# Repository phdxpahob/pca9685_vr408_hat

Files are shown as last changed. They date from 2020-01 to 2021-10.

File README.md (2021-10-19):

# pca9685_vr408

This is a Raspberry Pi Hat with PCA9685PW. Design is based on the original Adafruit 16-Channel 12-bit PWM/Servo Driver with I2C interface, adapted for velleman spider robots. 

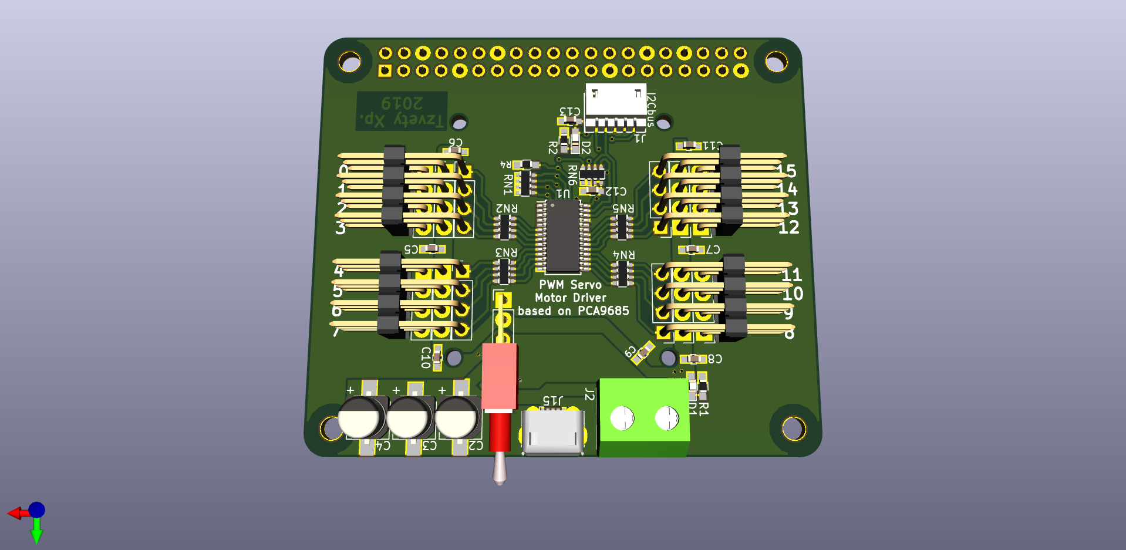
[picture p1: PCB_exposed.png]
PCB without camera stand
 

# WARNING

In revision A, there is an error in the design, VDD of the IC is not connected to the 3.3V rail of the Raspberry PI. This could be done using a wire bridge between the I2C Bus connector and the Via near C12. This is fixed in the current revision.

# Features and benefits:

- Both USB micro-B or terminal block power; 
- Can be powered directly from powerbank or another Pi HAT. 
- Split motor supply, extra capacitors to improve EMC. Tested with servos on all channels and the hat does not reset the Pi.
- Solder jumpers to change I2C address.
- Compatible with Adafruit libraries
- Header connects directly to the I2C pins & GPIO04 for O̅E̅ (Output enable). Even if GPIO is not configured the board is in output enable mode.
- Room for camera stand. (3D model is cam_stand.wrl)

# Limitations:

- No Reverse polarity protection! Keep in mind how you wire the terminal block!

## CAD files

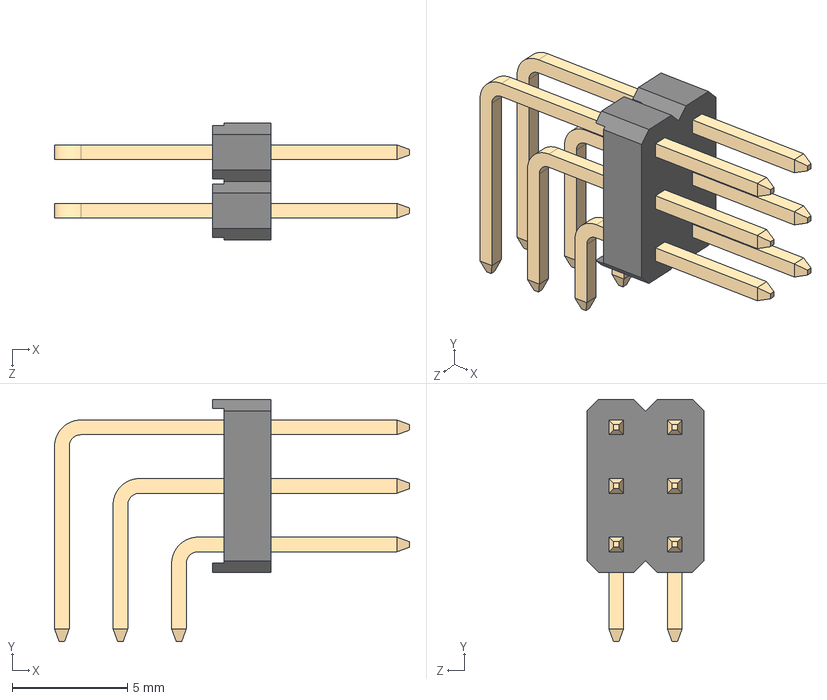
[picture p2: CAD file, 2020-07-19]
BB02-HL061-XB1-6030R0-6T_rev1.6.STEP
15.4 x 10.5 x 5.08 mm
BB02-HL - housing-6p
BB02-HL- Short RA type pin-A=6.0mm,B=3.0mm x 2
BB02-HL- Mid RA type pin-A=6.0mm,B=3.0mm x 2
BB02-HL-Long RA type pin-A=6.0mm,B=3.0mm x 2

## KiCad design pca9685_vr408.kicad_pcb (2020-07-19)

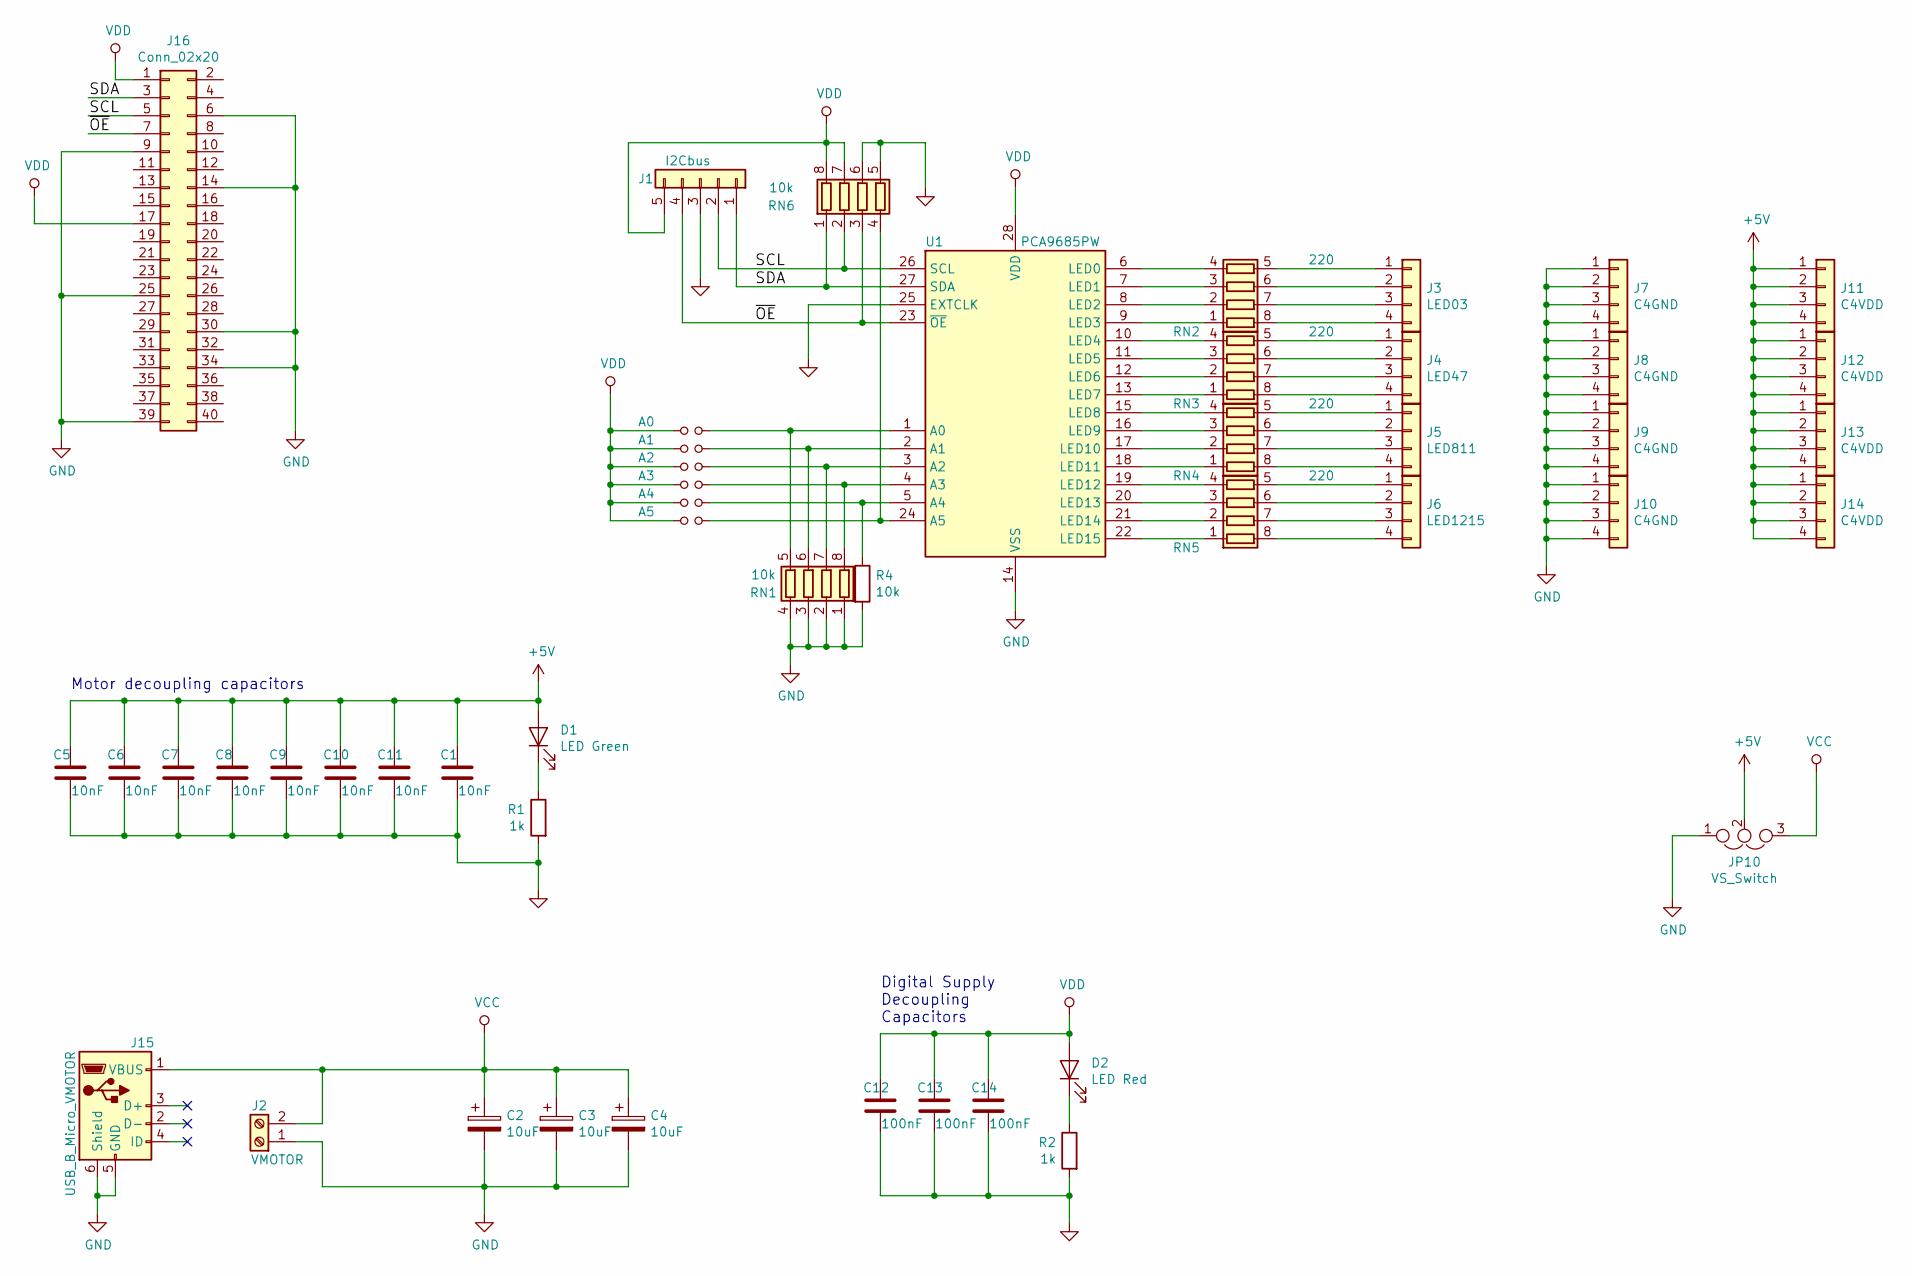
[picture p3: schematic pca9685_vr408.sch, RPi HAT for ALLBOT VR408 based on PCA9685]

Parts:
A0: A0; SolderJumper_Triangular_0603
A1: A1; SolderJumper_Triangular_0603
A2: A2; SolderJumper_Triangular_0603
A3: A3; SolderJumper_Triangular_0603
A4: A4; SolderJumper_Triangular_0603
A5: A5; SolderJumper_Triangular_0603
C1, C5, C6, C7, C8, C9, C10, C11: 10nF; C_0603_HandSoldering
C2, C3, C4: 10uF; CP_Elec_5x5.3
C12, C13, C14: 100nF; C_0603_HandSoldering
D1: LED Green; LED_0603_HandSoldering
D2: LED Red; LED_0603_HandSoldering
J1: I2Cbus; df13-5p-125ds
J2: VMOTOR; TerminalBlock_bornier-2_P5.08mm
J3: LED03; Pin_Header_Straight_1x04_Pitch2.54mm
J4: LED47; Pin_Header_Straight_1x04_Pitch2.54mm
J5: LED811; Pin_Header_Straight_1x04_Pitch2.54mm
J6: LED1215; Pin_Header_Straight_1x04_Pitch2.54mm
J7, J8, J9, J10: C4GND; Pin_Header_Straight_1x04_Pitch2.54mm
J11, J12, J13, J14: C4VDD; Pin_Header_Straight_1x04_Pitch2.54mm
J15: USB_B_Micro_VMOTOR; USB_Micro-B_Molex-105017-0001
J16: Conn_02x20; PinSocket_2x20_P2.54mm_Vertical
JP10: VS_Switch; Pin_Header_Straight_1x03_Pitch2.54mm
R1, R2: 1k; R_0603_HandSoldering
R4: 10k; R_0603_HandSoldering
RN1, RN6: 10k; R_Array_Convex_4x0603
RN2, RN3, RN4, RN5: 220; R_Array_Convex_4x0603
U1: PCA9685PW; TSSOP-28_4.4x9.7mm_Pitch0.65mm

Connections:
+5V: C1.1, C5.1, C6.1, C7.1, C8.1, C9.1, C10.1, C11.1, D1.2 (A), J11.1, J11.2, J11.3, J11.4, J12.1, J12.2, J12.3, J12.4, J13.1, J13.2, J13.3, J13.4, J14.1, J14.2, J14.3, J14.4, JP10.2
/SCL: J1.2, J16.5, RN6.2 (R2.1), U1.26 (SCL)
/SDA: J1.1, J16.3, RN6.1 (R1.1), U1.27 (SDA)
/~OE~: J1.4, J16.7, RN6.3 (R3.1), U1.23 (~OE)
GND: C1.2, C2.2, C3.2, C4.2, C5.2, C6.2, C7.2, C8.2, C9.2, C10.2, C11.2, C12.2, C13.2, C14.2, J1.3, J2.1, J7.1, J7.2, J7.3, J7.4, J8.1, J8.2, J8.3, J8.4, J9.1, J9.2, J9.3, J9.4, J10.1, J10.2, J10.3, J10.4, J15.5 (GND), J15.6 (Shield), J16.6, J16.9, J16.14, J16.25, J16.30, J16.34, J16.39, JP10.1, R1.2, R2.2, R4.2, RN1.1 (R1.1), RN1.2 (R2.1), RN1.3 (R3.1), RN1.4 (R4.1), RN6.5 (R4.2), RN6.6 (R3.2), U1.14 (VSS), U1.25 (EXTCLK)
unnamed: A0.2, RN1.5 (R4.2), U1.1 (A0)
unnamed: A1.2, RN1.6 (R3.2), U1.2 (A1)
unnamed: A2.2, RN1.7 (R2.2), U1.3 (A2)
unnamed: A3.2, RN1.8 (R1.2), U1.4 (A3)
unnamed: A4.2, R4.1, U1.5 (A4)
unnamed: A5.2, RN6.4 (R4.1), U1.24 (A5)
unnamed: D1.1 (K), R1.1
unnamed: D2.1 (K), R2.1
unnamed: J3.1, RN2.5 (R4.2)
unnamed: J3.2, RN2.6 (R3.2)
unnamed: J3.3, RN2.7 (R2.2)
unnamed: J3.4, RN2.8 (R1.2)
unnamed: J4.1, RN3.5 (R4.2)
unnamed: J4.2, RN3.6 (R3.2)
unnamed: J4.3, RN3.7 (R2.2)
unnamed: J4.4, RN3.8 (R1.2)
unnamed: J5.1, RN4.5 (R4.2)
unnamed: J5.2, RN4.6 (R3.2)
unnamed: J5.3, RN4.7 (R2.2)
unnamed: J5.4, RN4.8 (R1.2)
unnamed: J6.1, RN5.5 (R4.2)
unnamed: J6.2, RN5.6 (R3.2)
unnamed: J6.3, RN5.7 (R2.2)
unnamed: J6.4, RN5.8 (R1.2)
unnamed: RN2.1 (R1.1), U1.9 (LED3)
unnamed: RN2.2 (R2.1), U1.8 (LED2)
unnamed: RN2.3 (R3.1), U1.7 (LED1)
unnamed: RN2.4 (R4.1), U1.6 (LED0)
unnamed: RN3.1 (R1.1), U1.13 (LED7)
unnamed: RN3.2 (R2.1), U1.12 (LED6)
unnamed: RN3.3 (R3.1), U1.11 (LED5)
unnamed: RN3.4 (R4.1), U1.10 (LED4)
unnamed: RN4.1 (R1.1), U1.18 (LED11)
unnamed: RN4.2 (R2.1), U1.17 (LED10)
unnamed: RN4.3 (R3.1), U1.16 (LED9)
unnamed: RN4.4 (R4.1), U1.15 (LED8)
unnamed: RN5.1 (R1.1), U1.22 (LED15)
unnamed: RN5.2 (R2.1), U1.21 (LED14)
unnamed: RN5.3 (R3.1), U1.20 (LED13)
unnamed: RN5.4 (R4.1), U1.19 (LED12)
VCC: C2.1, C3.1, C4.1, J2.2, J15.1 (VBUS), JP10.3
VDD: A0.1, A1.1, A2.1, A3.1, A4.1, A5.1, C12.1, C13.1, C14.1, D2.2 (A), J1.5, J16.1, J16.17, RN6.7 (R2.2), RN6.8 (R1.2), U1.28 (VDD)

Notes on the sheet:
Motor decoupling capacitors
Digital Supply Decoupling Capacitors

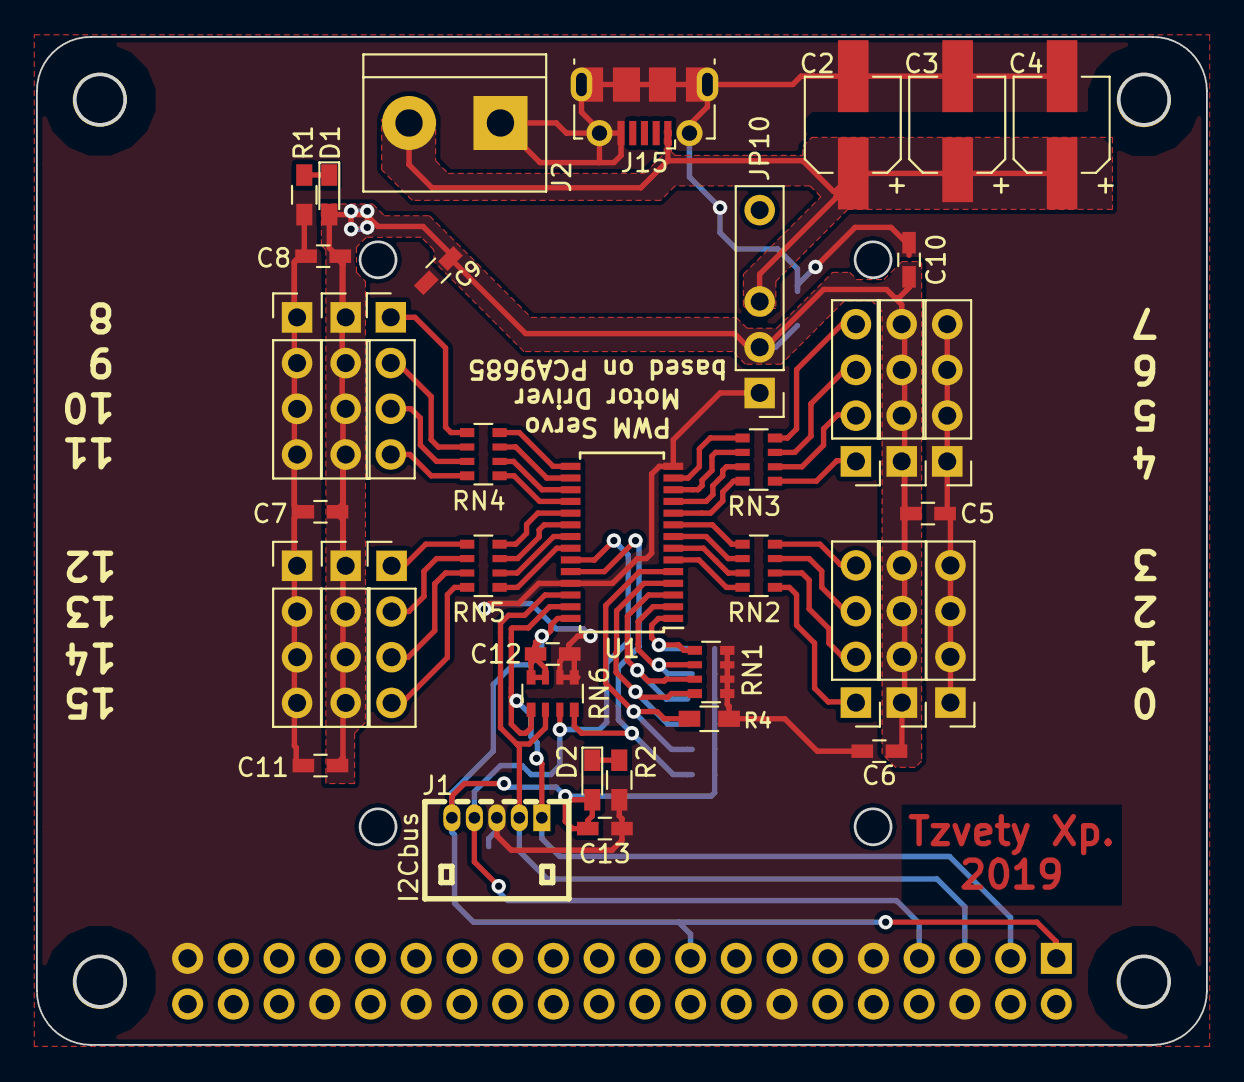
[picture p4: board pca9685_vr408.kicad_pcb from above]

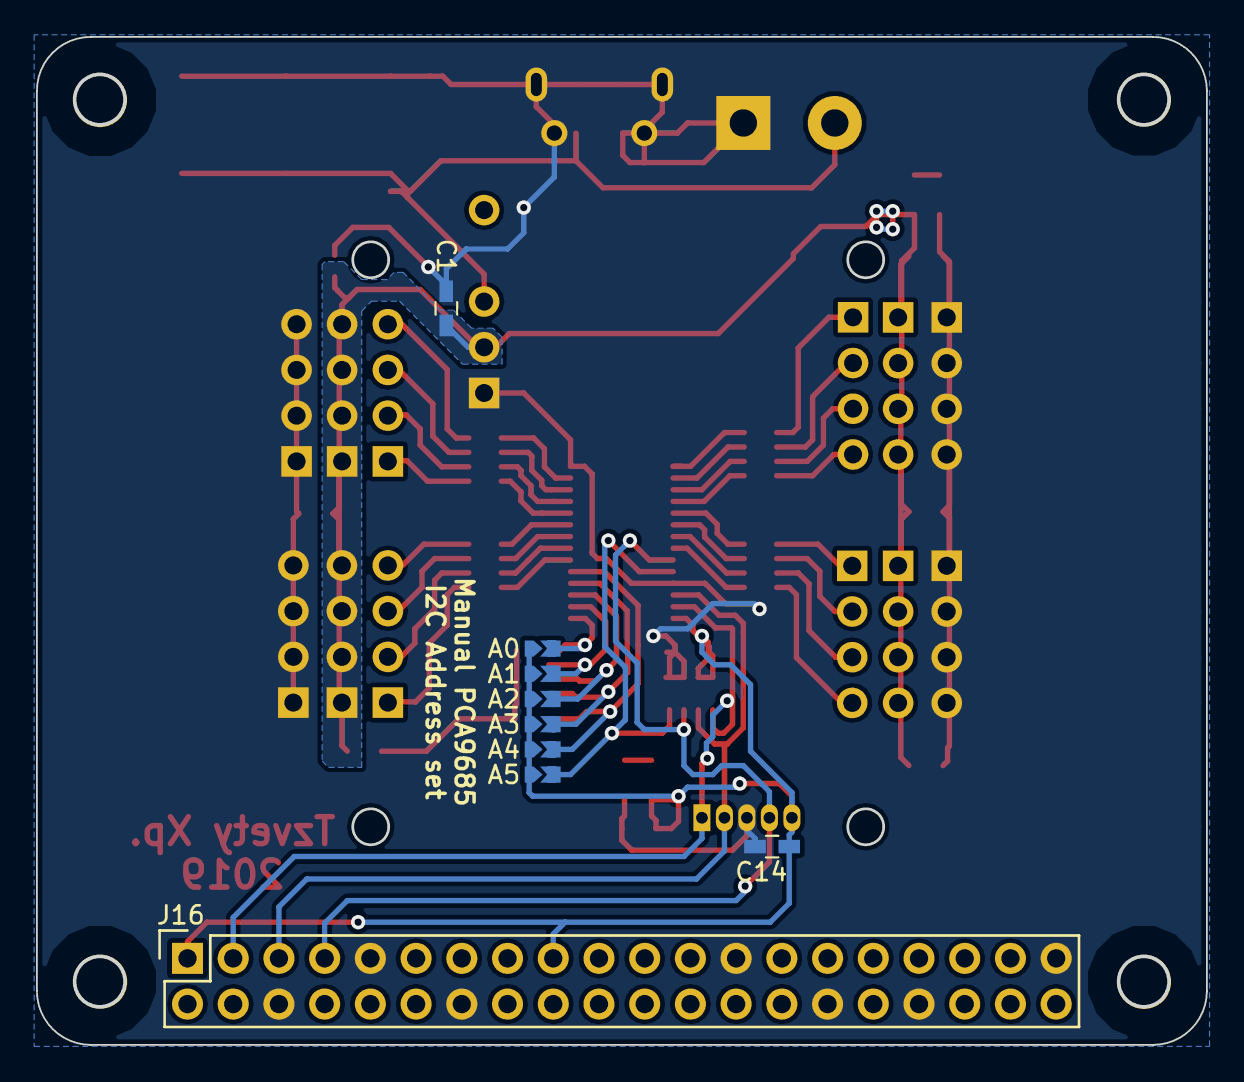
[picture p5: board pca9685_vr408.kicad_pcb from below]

Board: 2 copper layers, 65.0 x 56.0 mm, 53 parts (9 on the bottom side), 47 nets.

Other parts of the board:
H1, H2, H3, H4: 3mm_Mounting_Hole; NPTH_3mm_ID

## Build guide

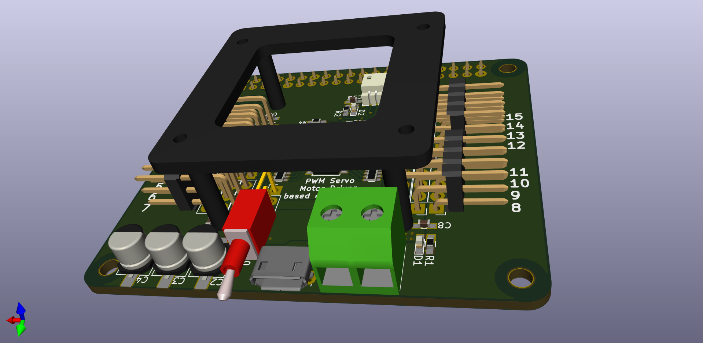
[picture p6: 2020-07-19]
PCB_full_assembly.png

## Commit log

2020-06-10 Updated layout
    [pca9685_vr412.sch, pca9685_vr412_2.kicad_pcb]
2021-10-19 Update README.md
    Add board picture and some text clarification.
